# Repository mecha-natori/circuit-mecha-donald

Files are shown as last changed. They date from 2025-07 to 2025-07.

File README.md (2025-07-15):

# メカドナルド

メカドナルドはSTM32F303ZDT6を使用したPWM MD駆動基板です。

エンコーダーを接続

## 仕様

| 機能 | 個数 | 備考 |
| :---: | ---: | :--- |
| MCU | 1 | STM32F303ZDT6 |
| ST-LINK | 1 | ピンアサインはSWD |
| CAN | 2 | 電源ピンは5V、Classic CANのみ対応、1系統から2個 |
| UART | 1 | 電源ピンは5V、USART1つ |
| PWM MD | 6 | 対応するエンコーダの端子と横並び |
| エンコーダ | 6 | 電源ピンは5V、対応するPWM MDの端子と横並び |
|  リセットスイッチ | 1 | |
| 5V-3.3Vレギュレータ | 1 | 外部電源からの供給用 |
| 寸法(外形) | | 111mm x 86mm |
| 寸法(ネジ穴間) | | 100mm x 75mm |

## 名前の由来

メカ+ドナルドです。他意はありません。 I'm burnin' it! (迫真)

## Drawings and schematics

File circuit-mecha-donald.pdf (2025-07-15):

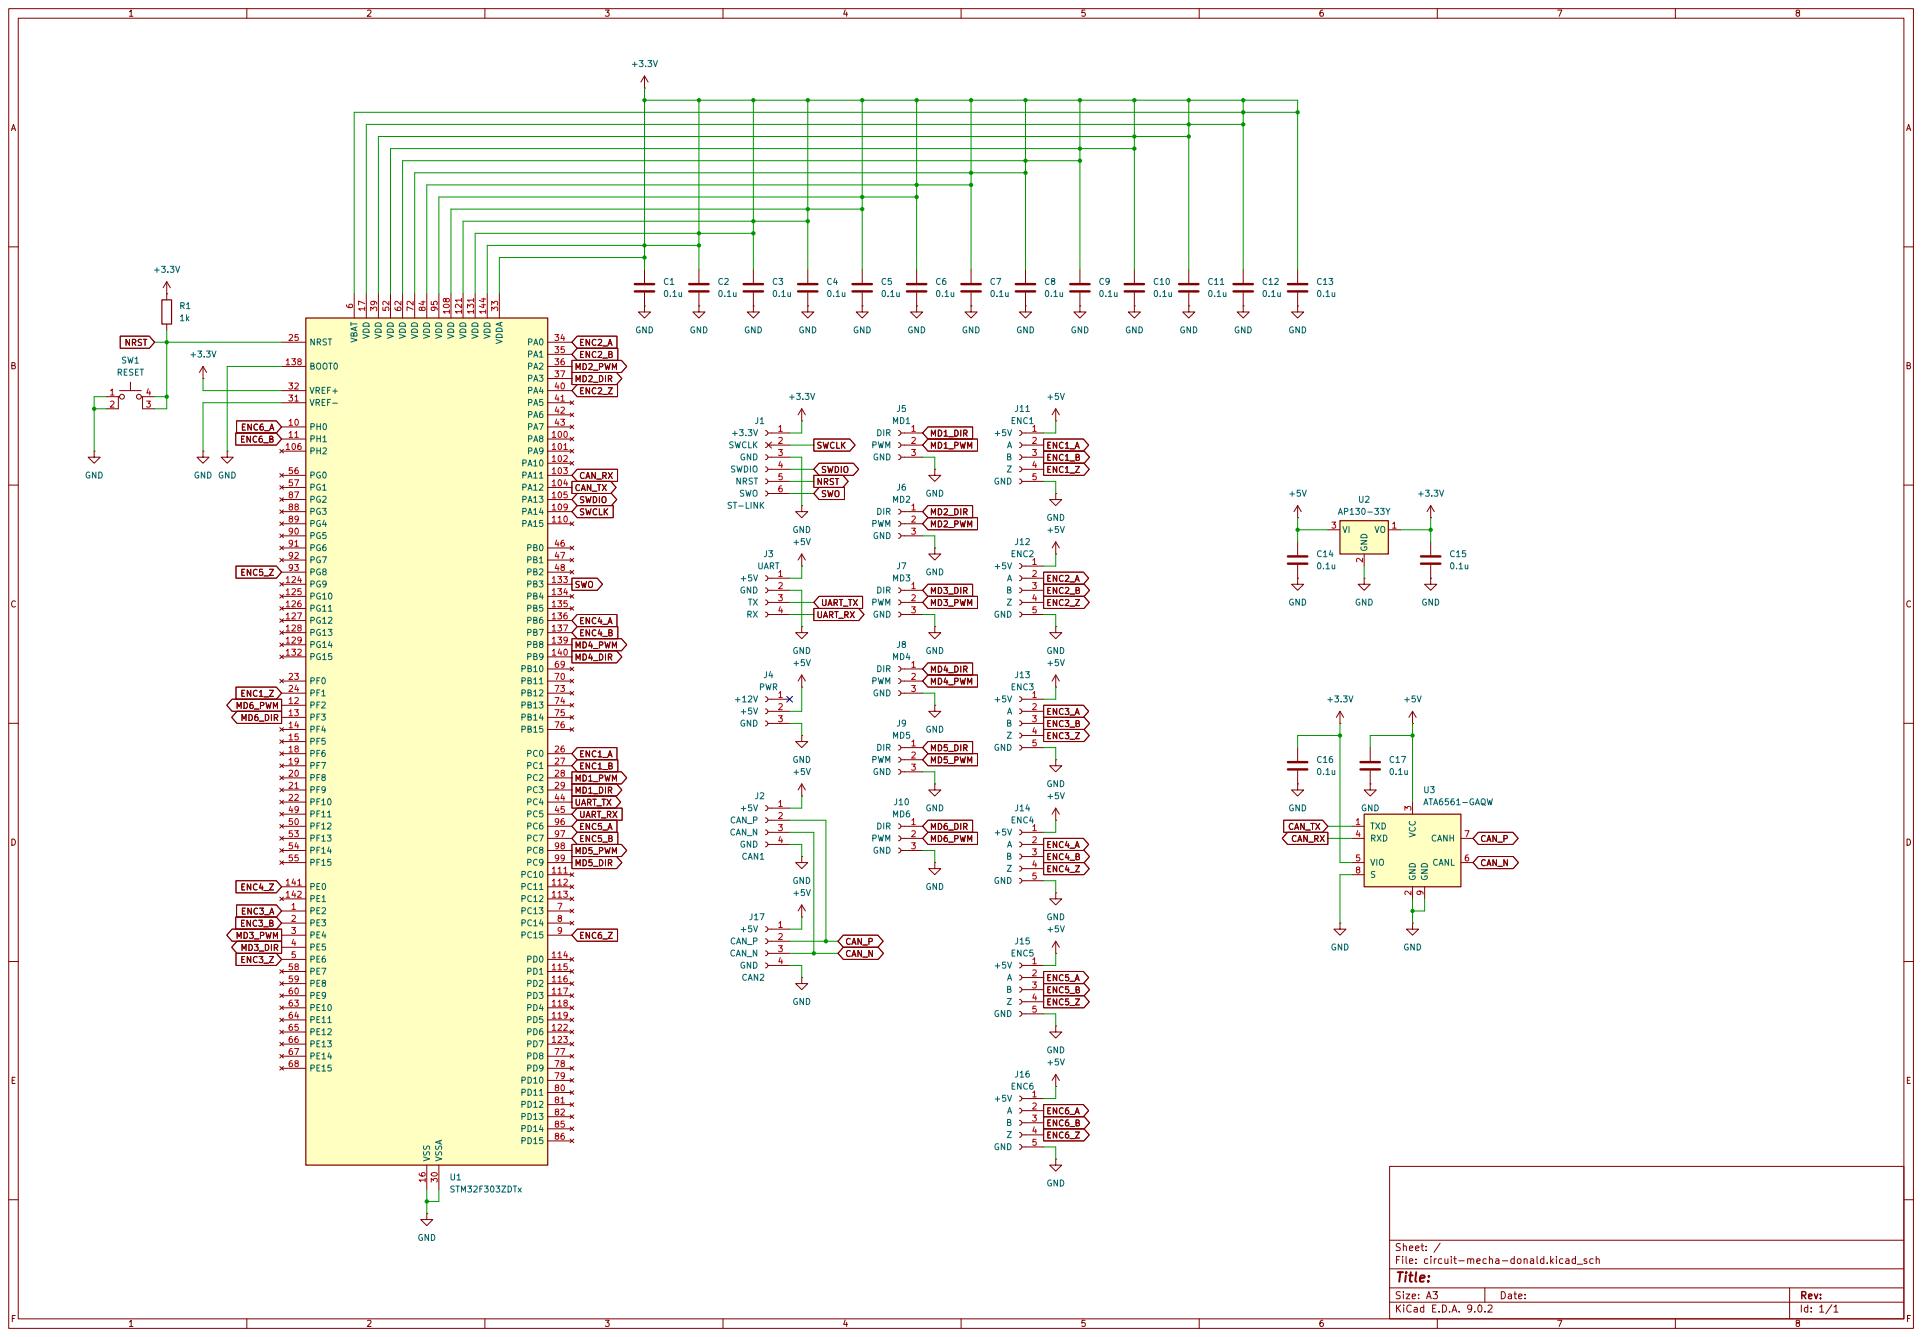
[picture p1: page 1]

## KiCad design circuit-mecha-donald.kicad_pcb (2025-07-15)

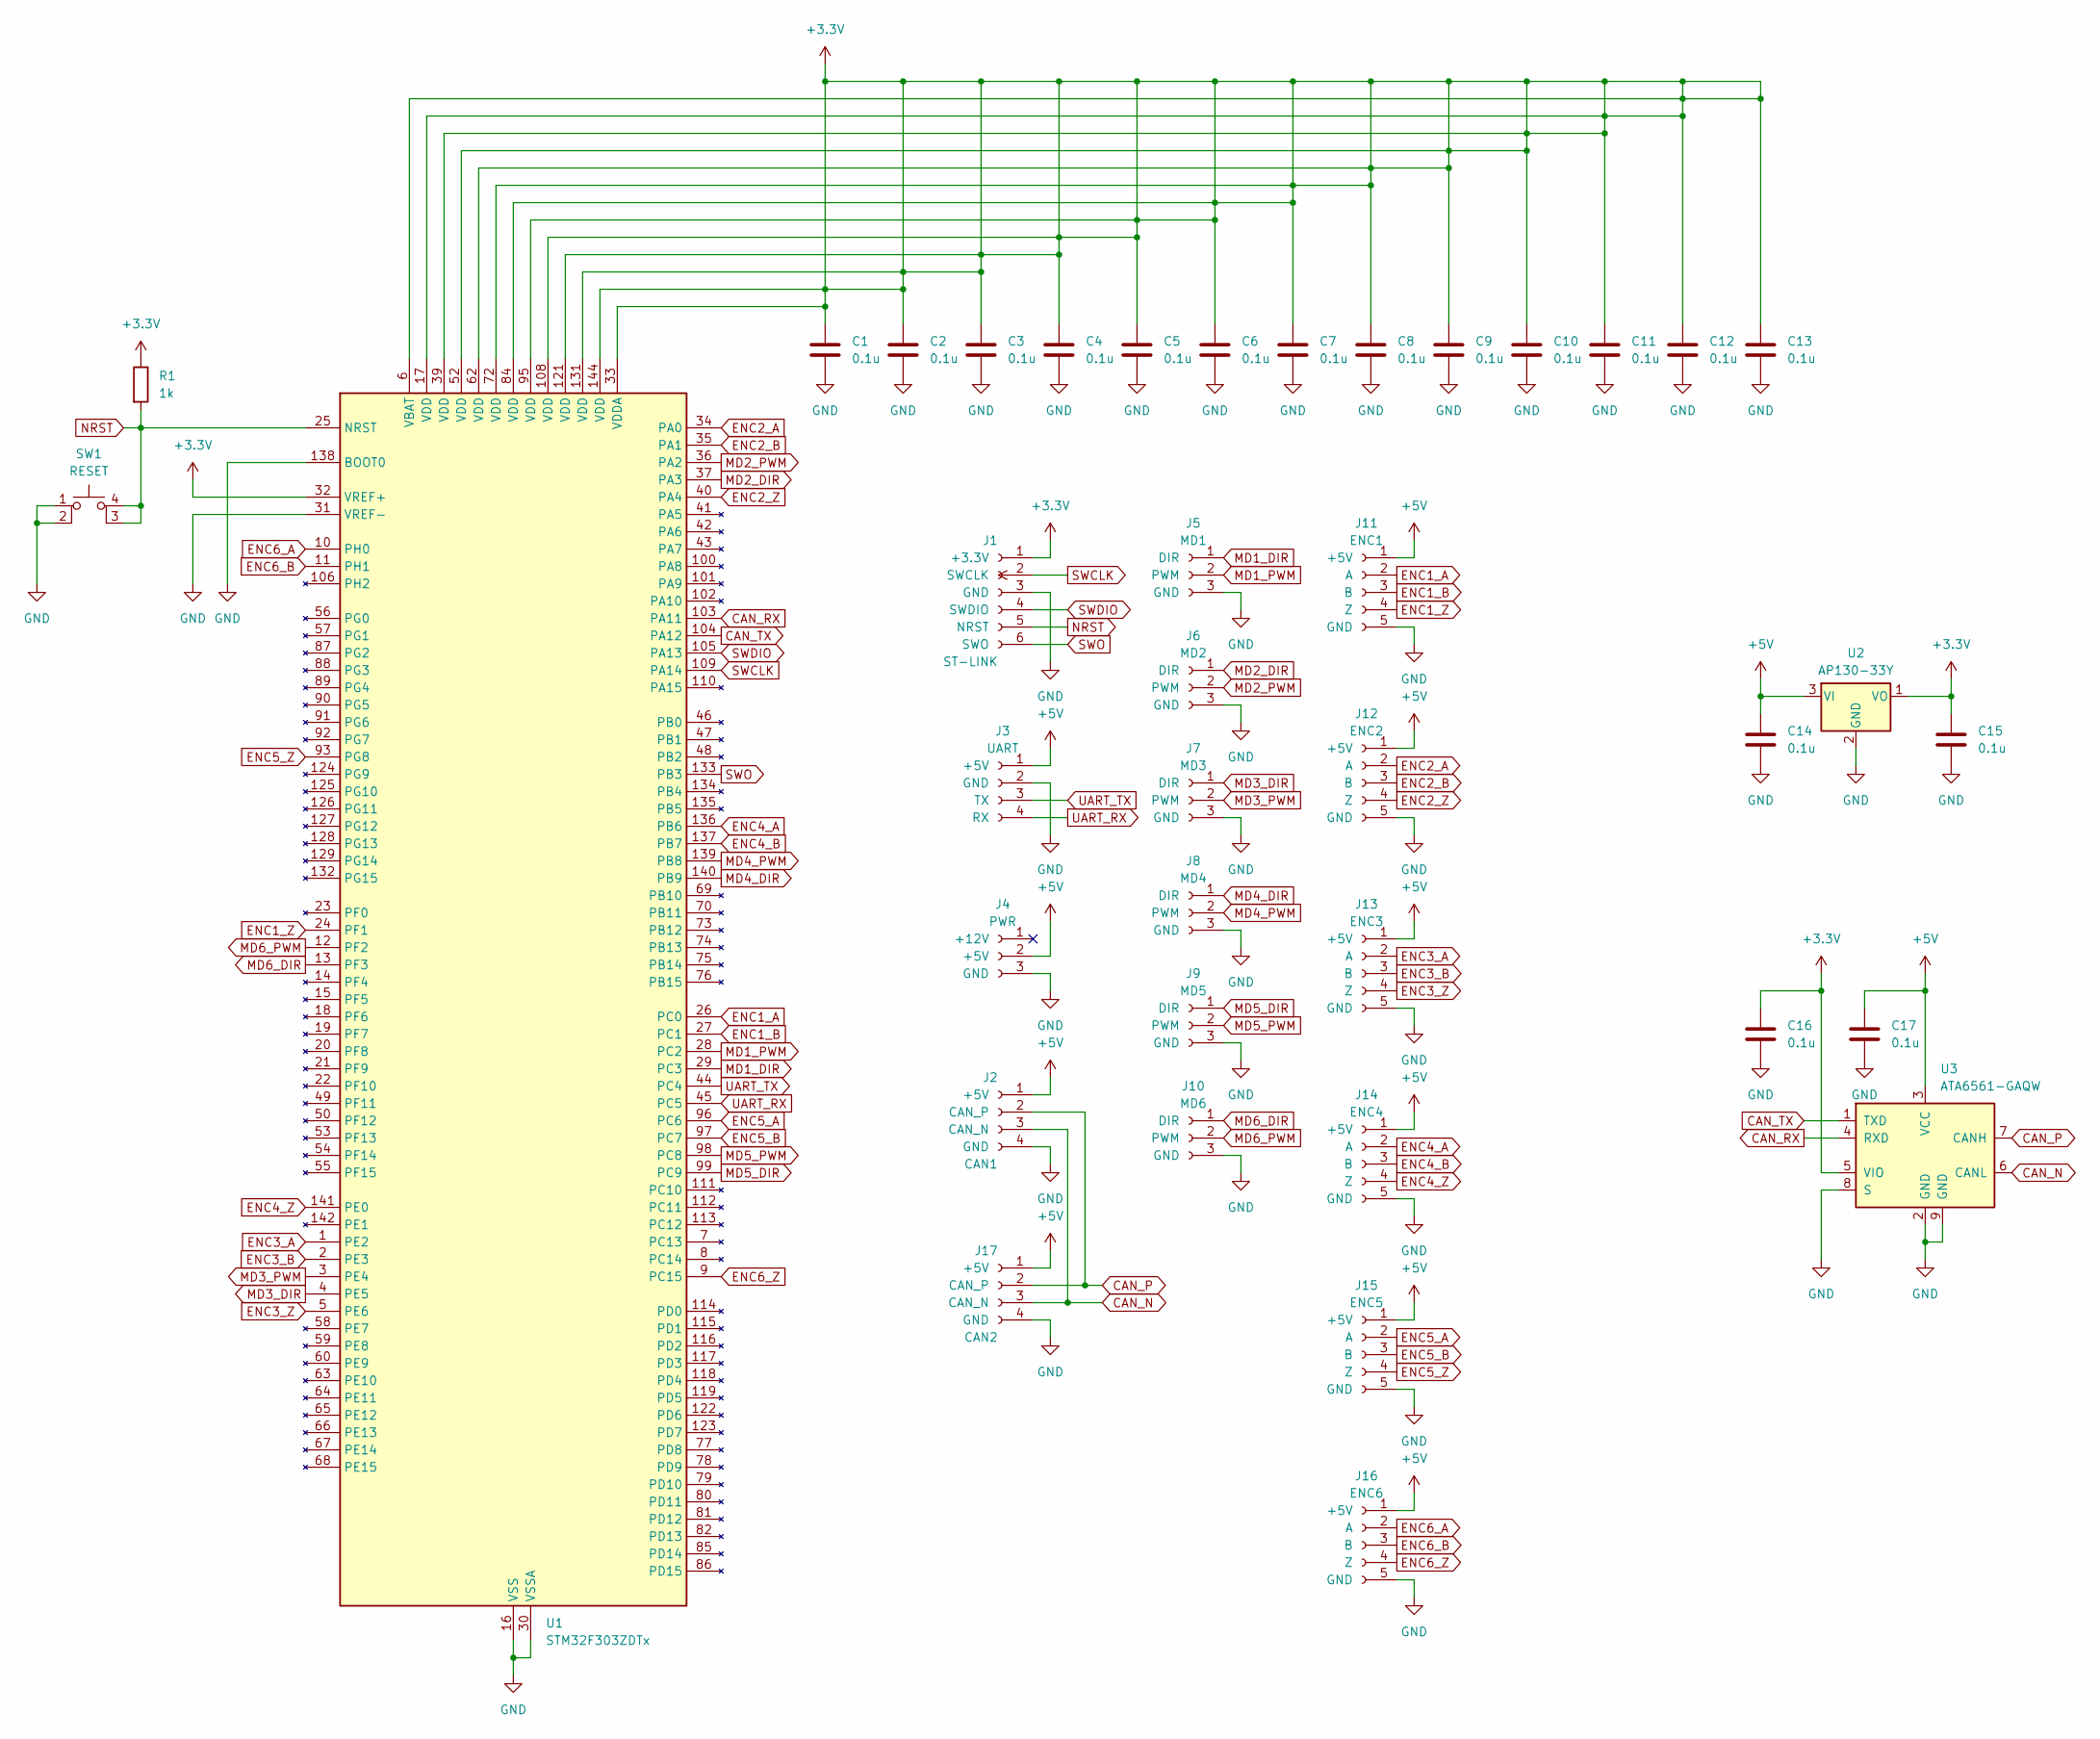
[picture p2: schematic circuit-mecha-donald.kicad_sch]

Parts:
C1, C2, C3, C4, C5, C6, C7, C8, C9, C10, C11, C12, C13, C14, C15, C16, C17: 0.1u; C_0603_1608Metric_Pad1.08x0.95mm_HandSolder
J1: ST-LINK; JST_ZH_B6B-ZR_1x06_P1.50mm_Vertical
J2: CAN1; JST_XA_B04B-XASK-1_1x04_P2.50mm_Vertical
J3: UART; DF1B-4P-2.5DSA
J4: PWR; JST_XH_B3B-XH-A_1x03_P2.50mm_Vertical
J5: MD1; JST_XA_B03B-XASK-1_1x03_P2.50mm_Vertical
J6: MD2; JST_XA_B03B-XASK-1_1x03_P2.50mm_Vertical
J7: MD3; JST_XA_B03B-XASK-1_1x03_P2.50mm_Vertical
J8: MD4; JST_XA_B03B-XASK-1_1x03_P2.50mm_Vertical
J9: MD5; JST_XA_B03B-XASK-1_1x03_P2.50mm_Vertical
J10: MD6; JST_XA_B03B-XASK-1_1x03_P2.50mm_Vertical
J11: ENC1; JST_PA_B05B-PASK-1_1x05_P2.00mm_Vertical
J12: ENC2; JST_PA_B05B-PASK-1_1x05_P2.00mm_Vertical
J13: ENC3; JST_PA_B05B-PASK-1_1x05_P2.00mm_Vertical
J14: ENC4; JST_PA_B05B-PASK-1_1x05_P2.00mm_Vertical
J15: ENC5; JST_PA_B05B-PASK-1_1x05_P2.00mm_Vertical
J16: ENC6; JST_PA_B05B-PASK-1_1x05_P2.00mm_Vertical
J17: CAN2; JST_XA_B04B-XASK-1_1x04_P2.50mm_Vertical
R1: 1k; R_0603_1608Metric_Pad0.98x0.95mm_HandSolder
SW1: RESET; tact
U1: STM32F303ZDTx; LQFP-144_20x20mm_P0.5mm
U2: AP130-33Y; SOT-89-3
U3: ATA6561-GAQW; SOIC-8-1EP_3.9x4.9mm_P1.27mm_EP2.95x4.9mm_Mask2.71x3.4mm

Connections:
+3.3V: C1.1, C2.1, C3.1, C4.1, C5.1, C6.1, C7.1, C8.1, C9.1, C10.1, C11.1, C12.1, C13.1, C15.1, C16.1, J1.1 (+3.3V), R1.1, U1.6 (VBAT), U1.17 (VDD), U1.32 (VREF+), U1.33 (VDDA), U1.39 (VDD), U1.52 (VDD), U1.62 (VDD), U1.72 (VDD), U1.84 (VDD), U1.95 (VDD), U1.108 (VDD), U1.121 (VDD), U1.131 (VDD), U1.144 (VDD), U2.1 (VO), U3.5 (VIO)
+5V: C14.1, C17.1, J2.1 (+5V), J3.1 (+5V), J4.2 (+5V), J11.1 (+5V), J12.1 (+5V), J13.1 (+5V), J14.1 (+5V), J15.1 (+5V), J16.1 (+5V), J17.1 (+5V), U2.3 (VI), U3.3 (VCC)
CAN_N: J2.3 (CAN_N), J17.3 (CAN_N), U3.6 (CANL)
CAN_P: J2.2 (CAN_P), J17.2 (CAN_P), U3.7 (CANH)
CAN_RX: U1.103 (PA11), U3.4 (RXD)
CAN_TX: U1.104 (PA12), U3.1 (TXD)
ENC1_A: J11.2 (A), U1.26 (PC0)
ENC1_B: J11.3 (B), U1.27 (PC1)
ENC1_Z: J11.4 (Z), U1.24 (PF1)
ENC2_A: J12.2 (A), U1.34 (PA0)
ENC2_B: J12.3 (B), U1.35 (PA1)
ENC2_Z: J12.4 (Z), U1.40 (PA4)
ENC3_A: J13.2 (A), U1.1 (PE2)
ENC3_B: J13.3 (B), U1.2 (PE3)
ENC3_Z: J13.4 (Z), U1.5 (PE6)
ENC4_A: J14.2 (A), U1.136 (PB6)
ENC4_B: J14.3 (B), U1.137 (PB7)
ENC4_Z: J14.4 (Z), U1.141 (PE0)
ENC5_A: J15.2 (A), U1.96 (PC6)
ENC5_B: J15.3 (B), U1.97 (PC7)
ENC5_Z: J15.4 (Z), U1.93 (PG8)
ENC6_A: J16.2 (A), U1.10 (PH0)
ENC6_B: J16.3 (B), U1.11 (PH1)
ENC6_Z: J16.4 (Z), U1.9 (PC15)
GND: C1.2, C2.2, C3.2, C4.2, C5.2, C6.2, C7.2, C8.2, C9.2, C10.2, C11.2, C12.2, C13.2, C14.2, C15.2, C16.2, C17.2, J1.3 (GND), J2.4 (GND), J3.2 (GND), J4.3 (GND), J5.3 (GND), J6.3 (GND), J7.3 (GND), J8.3 (GND), J9.3 (GND), J10.3 (GND), J11.5 (GND), J12.5 (GND), J13.5 (GND), J14.5 (GND), J15.5 (GND), J16.5 (GND), J17.4 (GND), SW1.1, SW1.2, U1.16 (VSS), U1.30 (VSSA), U1.31 (VREF-), U1.38 (VSS), U1.51 (VSS), U1.61 (VSS), U1.71 (VSS), U1.83 (VSS), U1.94 (VSS), U1.107 (VSS), U1.120 (VSS), U1.130 (VSS), U1.138 (BOOT0), U1.143 (VSS), U2.2 (GND), U3.2 (GND), U3.8 (S), U3.9 (GND)
MD1_DIR: J5.1 (DIR), U1.29 (PC3)
MD1_PWM: J5.2 (PWM), U1.28 (PC2)
MD2_DIR: J6.1 (DIR), U1.37 (PA3)
MD2_PWM: J6.2 (PWM), U1.36 (PA2)
MD3_DIR: J7.1 (DIR), U1.4 (PE5)
MD3_PWM: J7.2 (PWM), U1.3 (PE4)
MD4_DIR: J8.1 (DIR), U1.140 (PB9)
MD4_PWM: J8.2 (PWM), U1.139 (PB8)
MD5_DIR: J9.1 (DIR), U1.99 (PC9)
MD5_PWM: J9.2 (PWM), U1.98 (PC8)
MD6_DIR: J10.1 (DIR), U1.13 (PF3)
MD6_PWM: J10.2 (PWM), U1.12 (PF2)
NRST: J1.5 (NRST), R1.2, SW1.3 (K), SW1.4 (A), U1.25 (NRST)
SWCLK: J1.2 (SWCLK), U1.109 (PA14)
SWDIO: J1.4 (SWDIO), U1.105 (PA13)
SWO: J1.6 (SWO), U1.133 (PB3)
UART_RX: J3.4 (RX), U1.45 (PC5)
UART_TX: J3.3 (TX), U1.44 (PC4)

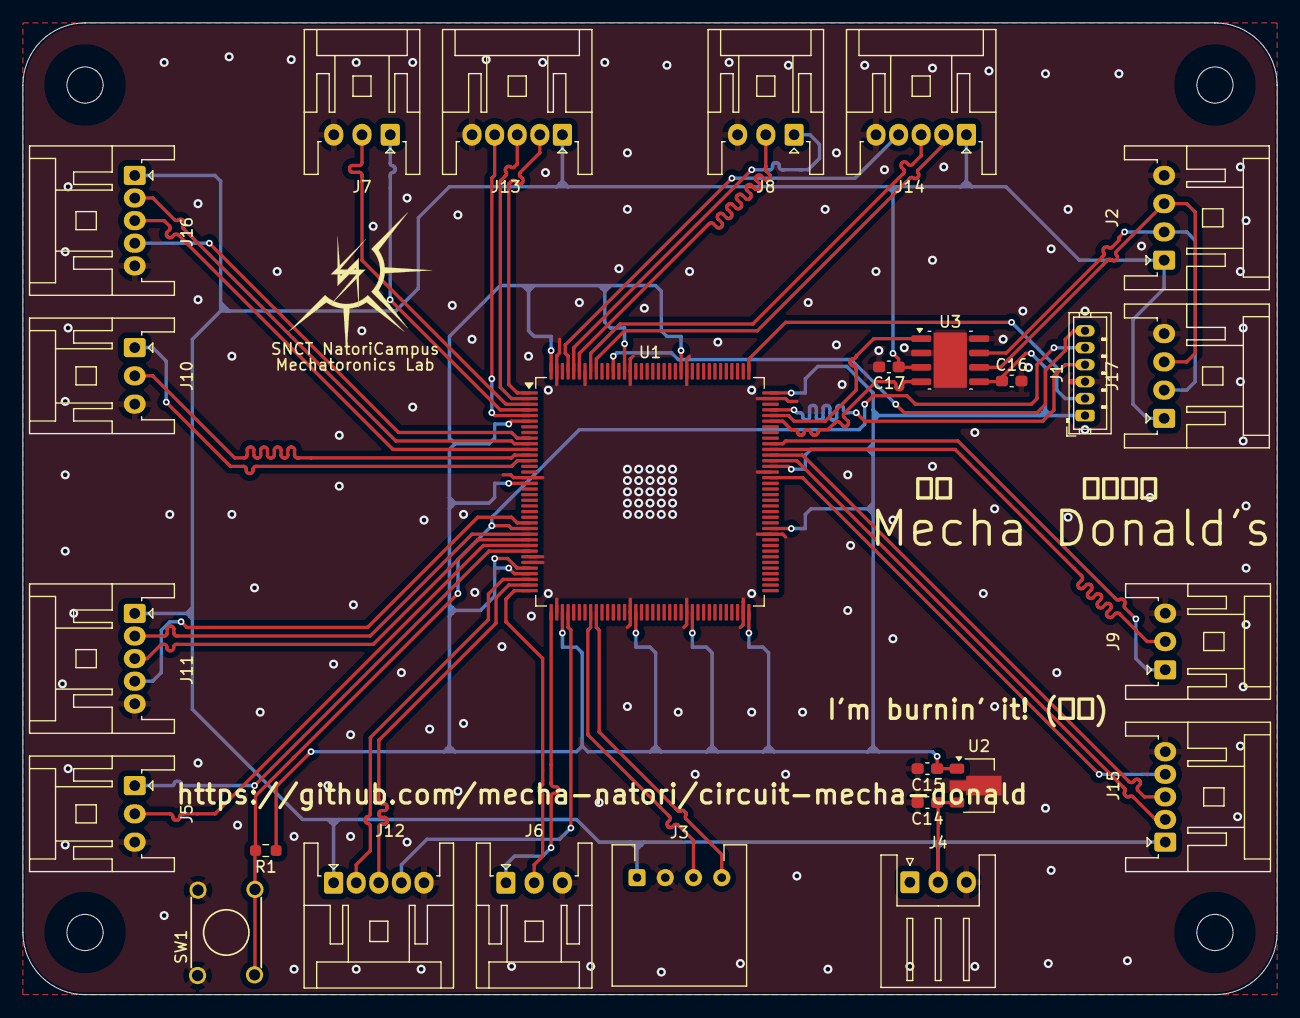
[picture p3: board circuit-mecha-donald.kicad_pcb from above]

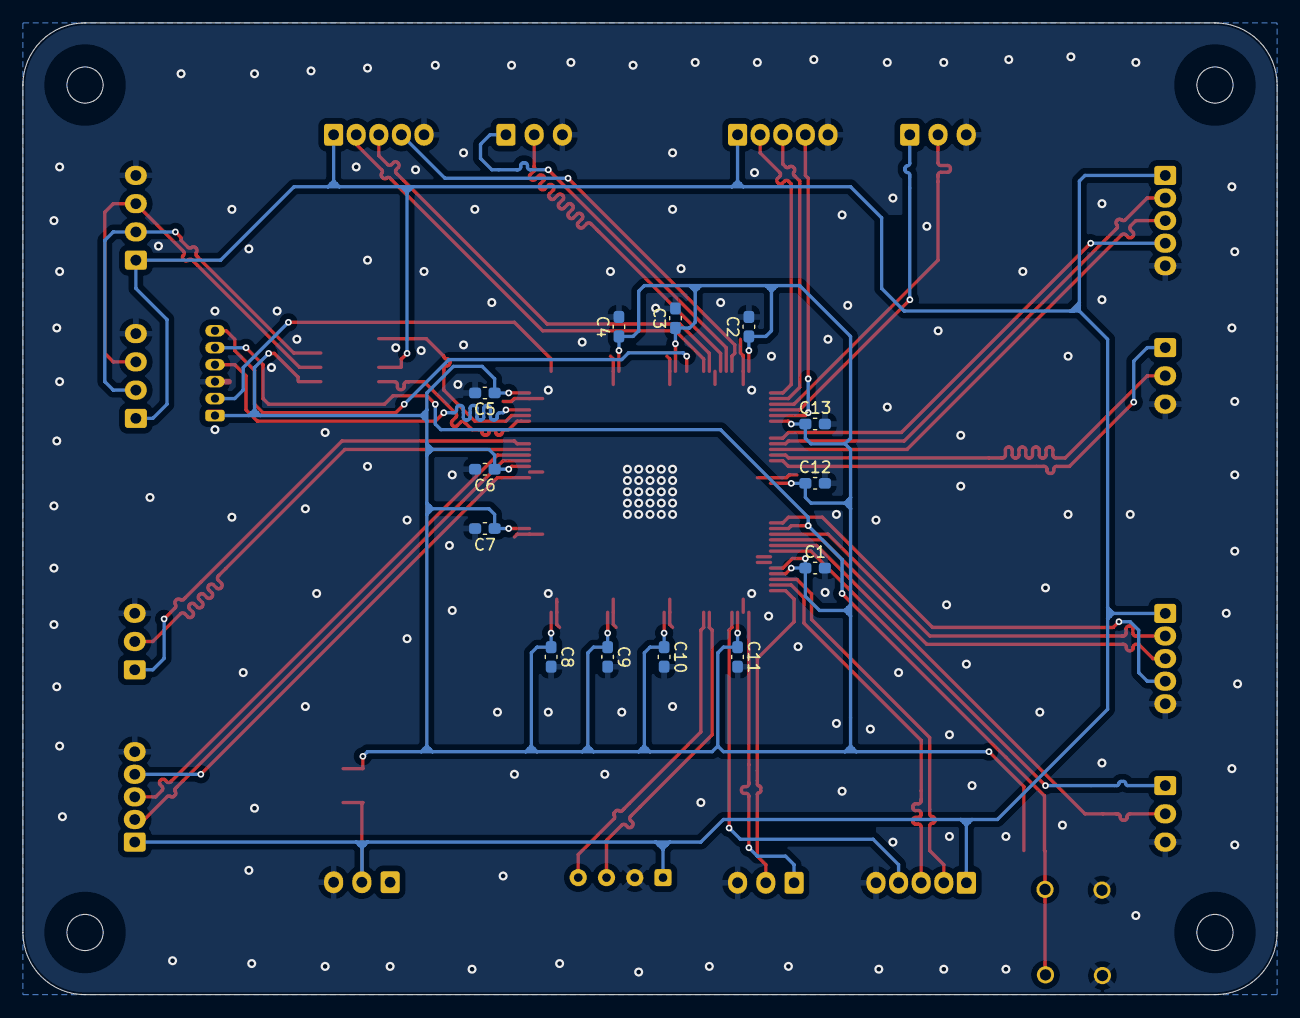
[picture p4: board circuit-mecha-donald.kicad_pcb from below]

Board: 2 copper layers, 111.0 x 86.0 mm, 43 parts (13 on the bottom side), 43 nets.

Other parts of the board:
 : holeφ3.2
 #2,  #3,  #4: holeφ3.2
